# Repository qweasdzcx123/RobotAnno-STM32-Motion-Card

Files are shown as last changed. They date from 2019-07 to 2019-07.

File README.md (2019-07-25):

# RobotAnno-STM32-Motion-Card
## RobotAnno robotic arm
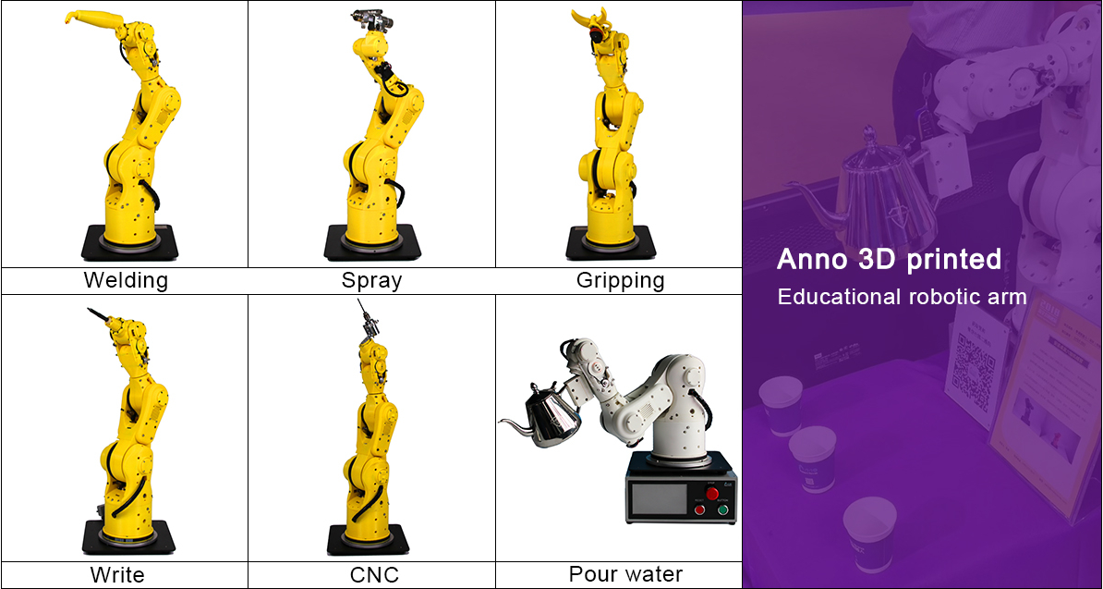
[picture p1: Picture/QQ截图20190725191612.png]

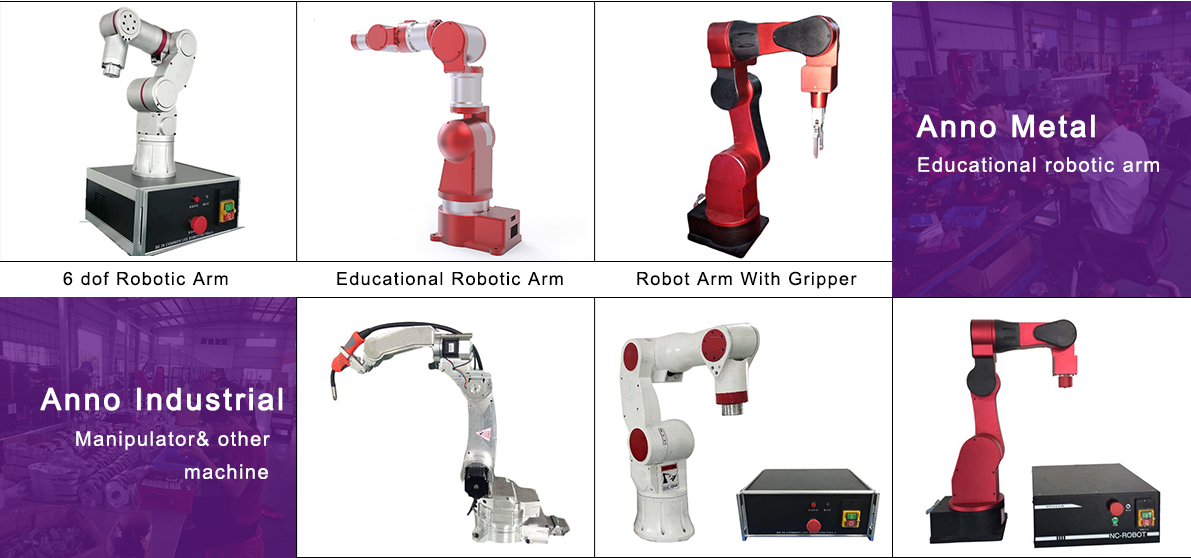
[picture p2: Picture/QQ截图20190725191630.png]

## shop for RobotAnno
https://robotanno.en.alibaba.com/

## introduction
  RobotAnno, a developer and manufacturer of desktop robotics solutions.Through continuous innovation, RobotAnno is committed to providing
educational robots, light industrial robots and service robots with acost-effective, easy-to-use, and best-of-breed revolutionary desktop robot arm product and solution. RobotAnno Robotics Located at the scientific community of academies and makers of desktop robotics, the Robot Anno arm covers the areas of STEAM (science, technology, engineering, math),getting hands-on and hands-on experience in mechanics, electronics , The charm of control systems and computer science. RobotAnno strive to become China and the world's most influential desktop arm business.
## Product Features：
>> Cost-Effective
>>> To meet the same performance,will be the lowest price in the same level,RobotAnno robot arm price level can do a thousand dollars.High performance,called the best of small industrial robotic arm

>> High precision
>>> Multi-axis interpolation control algorithm to ensure that robots with high-precision control

>> Industrial  materials
>>> Using industrial materials as the robot body

>> Multi-function
>>> Support PC, and other intelligent interactive control methods

>> Rich secondary development interface
>>> Provide a serial port,and other rich communication for secondary development
## Control upper computer
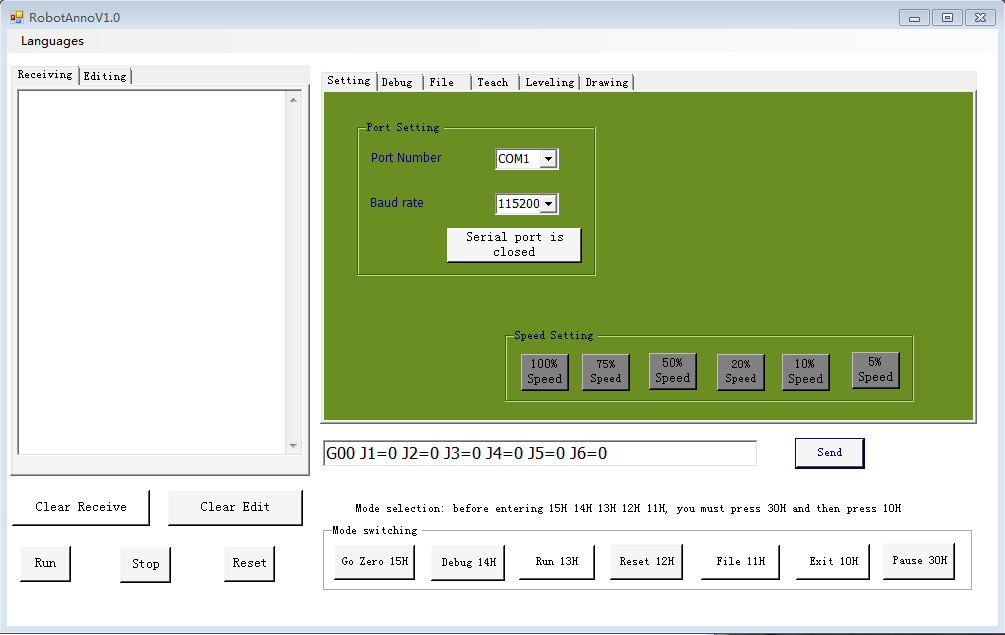
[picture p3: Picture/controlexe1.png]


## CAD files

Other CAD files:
CAD/RobotAnnoV6PLUS_2018-8.STEP
CAD/RobotAnnoV6PLUS_2018-8.SLDPRT

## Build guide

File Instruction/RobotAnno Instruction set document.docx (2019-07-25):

/************************************************* ******************************

* Hardware version: CoreV4D2, BASE-BOARDV61, IO-BOARDV6.2;

* System version: 180521 __lFQY_Core.hex

* Created: 2017.05.04

* Modified time: 2011.06.26

* Author:

* Update content: Cancel G04 command, cancel G24 command,

Increase G00 command, immediate value of absolute value, variable; incremental immediate value, variable

Add 2 formats (angle and radians) Trigonometric operation instructions SIN, COS, TAN, ASIN, ASOS, ATAN

************************************************** *****************************/

1. Serial port instruction

1.1 serial port mode

Serial port parameters: baud rate 115200; data bit 8; stop bit 1.

Instruction format:

The control commands are hexadecimal 0X10 (idle mode), 0X11 (file mode), 0X12 (zero return mode), 0X13 (run mode), 0X14 (debug mode), 0X15 (reset mode); 0X05 is the interrogation mode;

The running instructions all start with 'GXX' and end with a carriage return;

The teaching instruction ends with a carriage return and a new line;

In the system version of 180521 and above, when _flagSoftRst=1 is set in the parameter file, the serial port 1 can send 0X18 to output the output port o14 in any case. According to this function, the e14 relay control NRST restart (emergency stop).

0X05: == query mode ==

The control card is in any working mode (except file mode), and the serial port sends 0X05 to ask the current working mode of the control card. The return value is 0X10, 0X12, 0X13, 0X14, 0X15.

0X10: == enter idle mode ==

When the control card is in idle mode (0X10): it is in idle mode.

In file mode, 0X10 is valid after the file operation instruction is run.

In the zero return mode, the robot stops moving (send 0X30) and sends 0X10 to take effect.

In the running mode, the robot stops moving (send 0X30) and sends 0X10 to take effect.

In reset mode, the reset completes the brake and exits to idle mode. It is in idle mode when it is turned on.

0X11: == enter file mode ==

Download the running file and select “Send File” after sending 0X11. Among them, the first act in the file

"wr=ST" is the run file;

"WR=INI" is a parameter file;

"WR=oq" is a zero return file;

"WR=T_0" is the default run file, equivalent to "wr=ST";

"WR=T_1" is the run 1 file;

"WR=T_2" is the run 2 file;

"WR=T_120" is the run 120 file;

The second behavior file name; the third behavior file length, the length is the file size except the first three lines.

After reading the running file and sending 0X11, send "WR=R,##" ("##" is the length of the read content) to receive the running file.

After reading the parameter file, send "WR=P,##" ("##" is the length of the read content) after sending 0X11 to receive the parameter file.

After reading the parameter file, after sending 0X11, send "WR=Q,##" ("##" is the length of the read content) to receive the zero return file.

The read parameter file can receive the run 0 file after sending 0X11 and sending "WR=H_0,##" ("##" is the read content length).

After reading the parameter file, send "WR=H_1,##" ("##" is the length of the read content) after sending 0X11 to receive the run 1 file.

After reading the parameter file, after sending 0X11, send "WR=H_120,##" ("##" is the read content length) to receive the run 120 file.

0X12: == Motor zero return mode ==

After entering the zero return mode, the system automatically runs the file content and the instructions sent by the serial port in real time. Pause is 0X30, continue to 0X12, exit is 0X10

Instructions can be obtained from the run file and can also be obtained from the serial port.

Automatically exit idle mode after running the contents of the file

0X13: == enter running mode ==

After entering the running mode, the system automatically runs the file content and the instructions sent by the serial port in real time. The pause is 0X30, the continuation is 0X13, and the exit is 0X10.

Instructions can be obtained from the run file and can also be obtained from the serial port.

After running the contents of the file, it automatically runs from the beginning.

0X14: == enter debug mode ==

Send 0X05 as the inquiry mode.

Send 0X10 as the exit mode.

Send "0" to stop and send the angle of each axis of the machine.

Send "SVON=1" for servo enable.

Send "SVON=0" to disable the servo.

Send "SVBM=1" to the servo without holding the brake.

Send "SVBM=0" as the servo brake.

Send "CLR=ST_PUL" to clear the position of the control card.

Send "CLR=SV_ALM" to clear the drive alarm.

Send "J#+" to the #axis angle plus motion (#=1, 2, 3, 4, 5, 6).

Send "J#-" to the ##axis angle minus motion.

Send "J#0" to stop at ##axis angle.

Send "J#<" to repeat the motion for the #axis angle (@0°~ -90°).

Send "J#>" to repeat the motion for the #axis angle (@ 0°~ 90°).

Send "P VE=####" to change the running speed to #### pulses/sec.

Send "P AC=####" to change the acceleration to #### pulses/square sec.

Send "P DE=####" to change the deceleration to #### pulses/square sec.

Send "G00 J#=####,...." to get the robot joints to the appropriate angle.

Send "G07 **=####" to specify parameters for changing the robot.

TX+: Cartesian coordinates X+;

TX-: Cartesian coordinates X-;

TY+: Cartesian coordinates Y+;

TY-: Cartesian coordinates Y-;

TZ+: Cartesian coordinates Z+;

TZ-: Cartesian coordinates Z-;

TA+: Cartesian coordinates A+;

TA-: Cartesian coordinates A-;

TB+: Cartesian coordinates B+;

TB-: Cartesian coordinates B-;

TC+: Cartesian coordinates C+;

TC-: Cartesian coordinates C-;

P CYCP1=800000: The J1 axis is subdivided into 800,000 pulses per week

P J1=24000 Assignment to J1

P=VE Query VE value There are VE, AC, DE, CYCP1,...,J1,...,H0,D1,H2...

0X15: == enter reset mode ==

Return the machine to zero.

2. Button control instructions

When starting up, press the "Start" button to run the robot to run mode.

In the operating mode, at runtime, press the "Stop" button to pause the machine.

In the operating mode, when stopped, press the "Start" button and the machine continues to run.

In the operation mode, when stopping, press the "Stop" button and then press the "Start" button, the machine resets and exits the idle mode.

Instruction description:

//========================================================= ===============

G0n=GGN such as G06 O=P1.1 is equivalent to GG6 O=P1.1

Point-to-point command G00, G20

G00 J1=0 J2=0 J3=-90 J4=0 J5=-90 J6=0 //with acceleration and deceleration absolute joint position command

G00 J1=VXX J2=0 J3=VXX J4=VXX J5=-90 J6=0 //With acceleration and deceleration Absolute joint position command

G00 ... J2'4 J3'VXX ... //with acceleration and deceleration relative joint position command

G00 ... J2'4 J3'VXX J4=VXX J5=-90... //J2 is

G20 X=300 Y=100 Z=500 A=0 B=180 C=0 D=0 //with acceleration and deceleration

G20 X=300 Y=VXX Z=VXX A=VXX B=180 C=VXX D=0 //with acceleration and deceleration

G30 EQ01 J1=UXXXX, J2=UXXXX, J3=UXXXX Read memory contents G30 EQ01 J1=U30100 J2=U30120 J3=U30140 J4=U30160

G30 EQ02 U3060=XX.XX Write memory contents G30 EQ02 U30500=10

G30 EQ03 ASK=UXXXX Query memory contents

G30 EQ04 Vxx=UXXXXXX

G30 EQ05 UXXXXXX=Vxx

G40 X=300 Y=100 Z=500 A=0 B=180 C=0 D=0 //No acceleration/deceleration

Linear command G01 G21

G01 J1=0 J2=0 J3=-90 J4=0 J5=-90 J6=0

G21 X=300 Y=100 Z=500 A=0 B=180 C=0 D=0

G21 X=VXX Y=VXX Z=500 A=0 B=VXX C=0 D=0

G41 X=300 Y=100 Z=500 A=0 B=180 C=0 D=0 //with acceleration and deceleration

G41 X=300 Y=VXX Z=VXX A=0 B=180 C=0 D=0 //with acceleration and deceleration

Arc command G02 G03 G04 G22 G23 G06 DEGREE=ARC (or degree)

When DEGREE=ARC is going to be a three-point arc

Current point: G21 X=200 Y=0 Z=200 A=-180 B=150 C=0 D=0

Second point: G22 X=300 Y=100 Z=200 A=-180 B=150 C=90 D=0

Third point: G23 X=400 Y=0 Z=200 A=-180 B=150 C=300 D=0

Arc running: G06 DEGREE=300

//========================================================= ===============

G06 directive

G06 T=500 delay 500 milliseconds

G06 t=VXX Delay VXX content milliseconds (for example: G08 MOV V400=#2000 G06 t=V400 is a delay of 2000 milliseconds)

G06 I=P1.1 Wait for P1 to be high

G06 I=P2.0 Wait for P2 to be low

G06 O=P1.1 makes output port P1 high (different port from input port)

G06 O=P2.0 makes the output port P2 low

G06 SCAN=I Read input port value, stored in V144-V150 unit

G06 SCAN=O Read output port value, stored in V160-V166 unit

G06 SCAN=RTC Read system clock value and store it in V176-V179 unit

G06 DEGREE=ARC robot takes a three-point arc

G06 DEGREE=35.2 The robot walks 35.2 degrees

G06 REPOS=J# J# Axis looks for HOME# sensor from angle increase direction (return to low level)

G06 REPOS=-J# J# axis finds HOME# sensor from angle reduction direction (return to low level)

G06 REPOS=J1 J1 axis finds HOME0 sensor from angle increase direction (return to low level)

G06 REPOS=-J1 J1 axis finds HOME0 sensor from angle reduction direction (return to low level)

G06 REPOS=JH# J# Axis finds HOME# sensor from angle increase direction (return to high level)

G06 REPOS=-JH# J# axis finds HOME# sensor from angle reduction direction (return to high level)

G06 REPOS=JH1 J1 axis finds HOME0 sensor from angle increase direction (return to high level)

G06 REPOS=-JH1 J1 axis finds HOME0 sensor from angle decrease direction (return to high level)

//========================================================= ===============

G07 command

G07 VE=250000 speed is 250,000 pulses per second

G07 AC=250000 Acceleration is 250,000 pulses per second squared

G07 DE=250000 Deceleration is 250,000 pulses per second squared

G07 VPP=250000 Maximum speed 250,000 pulses per second

G07 VP=20 Speed VE is 20% of the highest speed, VE=VPP*VP*0.01

G07 vp=VXX Speed VE is the content of the highest speed VXX, VE=VPP*VXX unit value *0.01

G07 _h0=xx height change

G07 RCM=1 print run command, 0 does not print run command

G07 GCM=1 is output at right angle coordinates when teaching, 0 is joint coordinate output

G07 MARKPOS_HERE X1=0 Y1=0 X2=100 Y2=100 Template MARK point

G07 MARKPOS X1=10 Y1=10 X2=110 Y2=110 Match MARK point

G07 UNIT=1.0 Interpolation accuracy (in mm)

G07 P J#=XXXX calibration J# axis

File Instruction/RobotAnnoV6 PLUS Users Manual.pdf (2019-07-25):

# Users Manual

# Prepare

## 1) Positioning before power-on

Manually place the machine in the vertical position as follows before turning the power on:

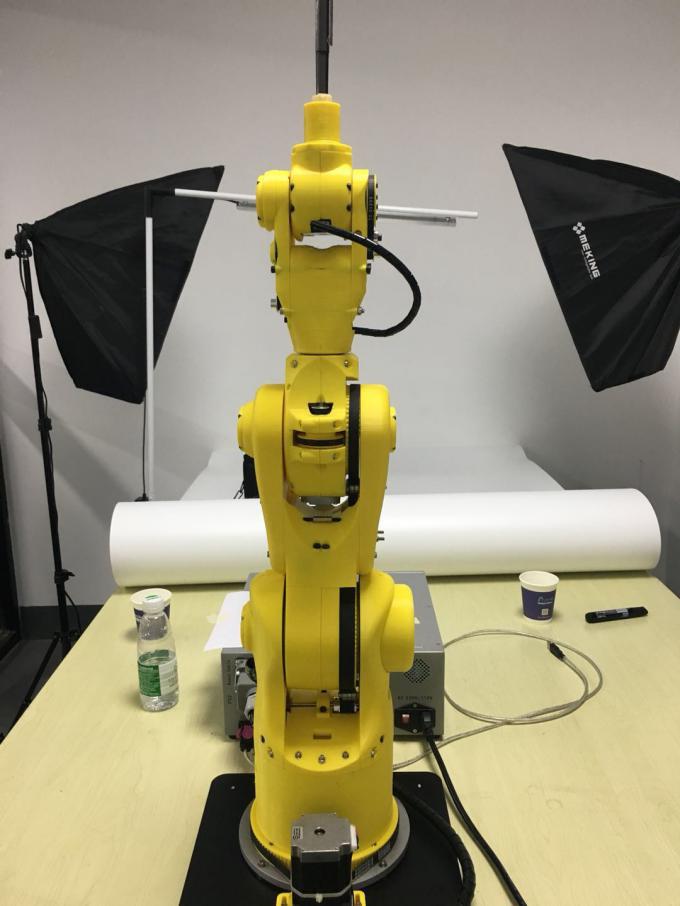
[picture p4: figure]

## 2）Joint position confirmation

After the placement is completed, pay attention to the alignment of the second joint and the third joint arrow, and try to ensure that the machine is in the vertical state, as shown in the following figure:

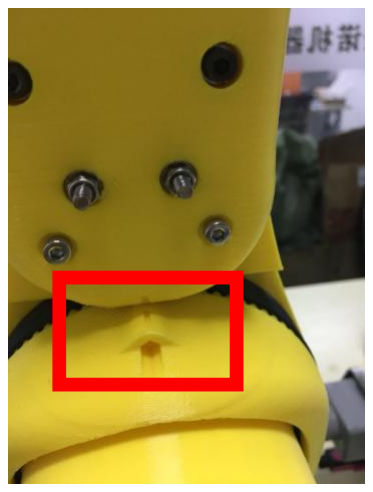
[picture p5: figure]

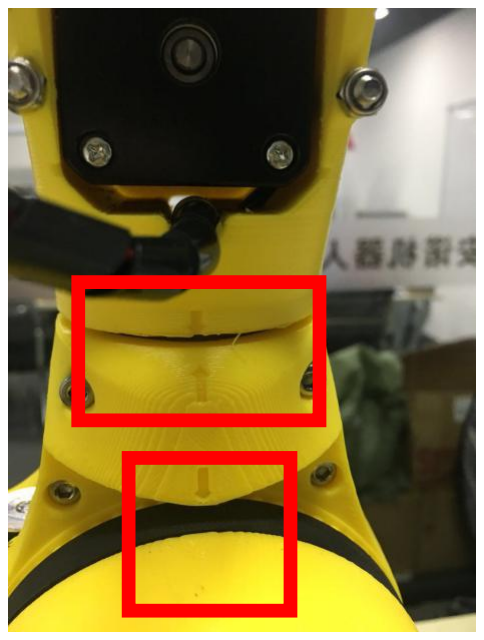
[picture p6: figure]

## 3）Direction confirmation

As shown in the figure below, first confirm whether the direction of each joint movement is consistent with the direction shown in the figure below. Before the machine is shipped from the factory, the direction parameter has been set to OK. If

the direction is inconsistent with the direction shown in the figure during the test, please reset the position of the robot after power off, and then test again. The direction of each joint of the robot must be ensured. Consistent.

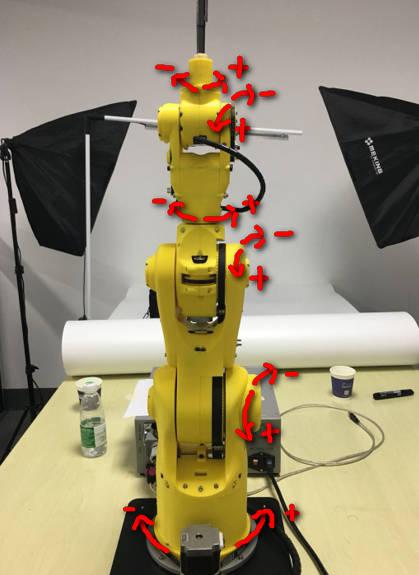
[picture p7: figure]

## 1. Establish a connection

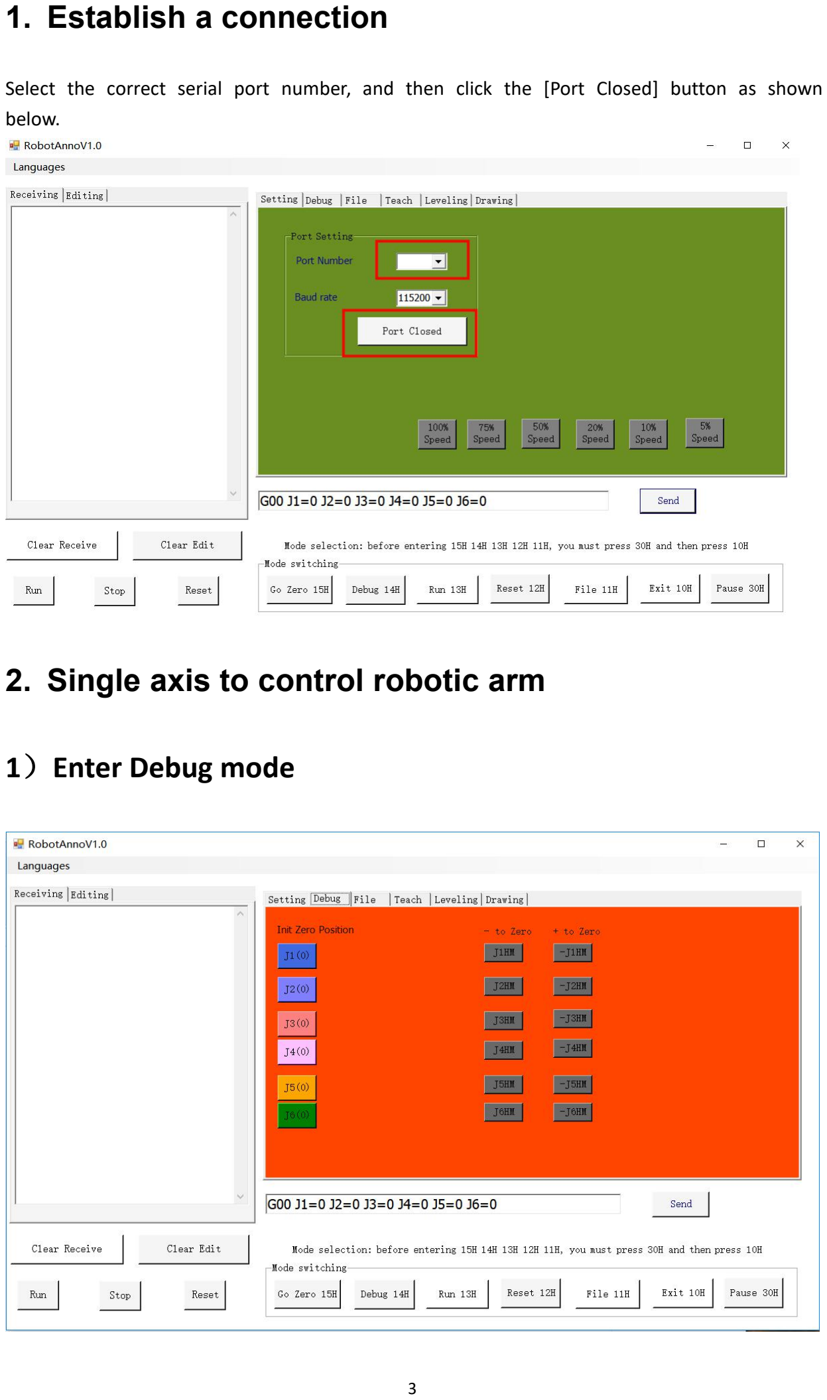
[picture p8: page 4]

Select the correct serial port number, and then click the [Port Closed] button as shown below.

## 2. Single axis to control robotic arm

## 1）Enter Debug mode

## 2）Initialize the position of each joint

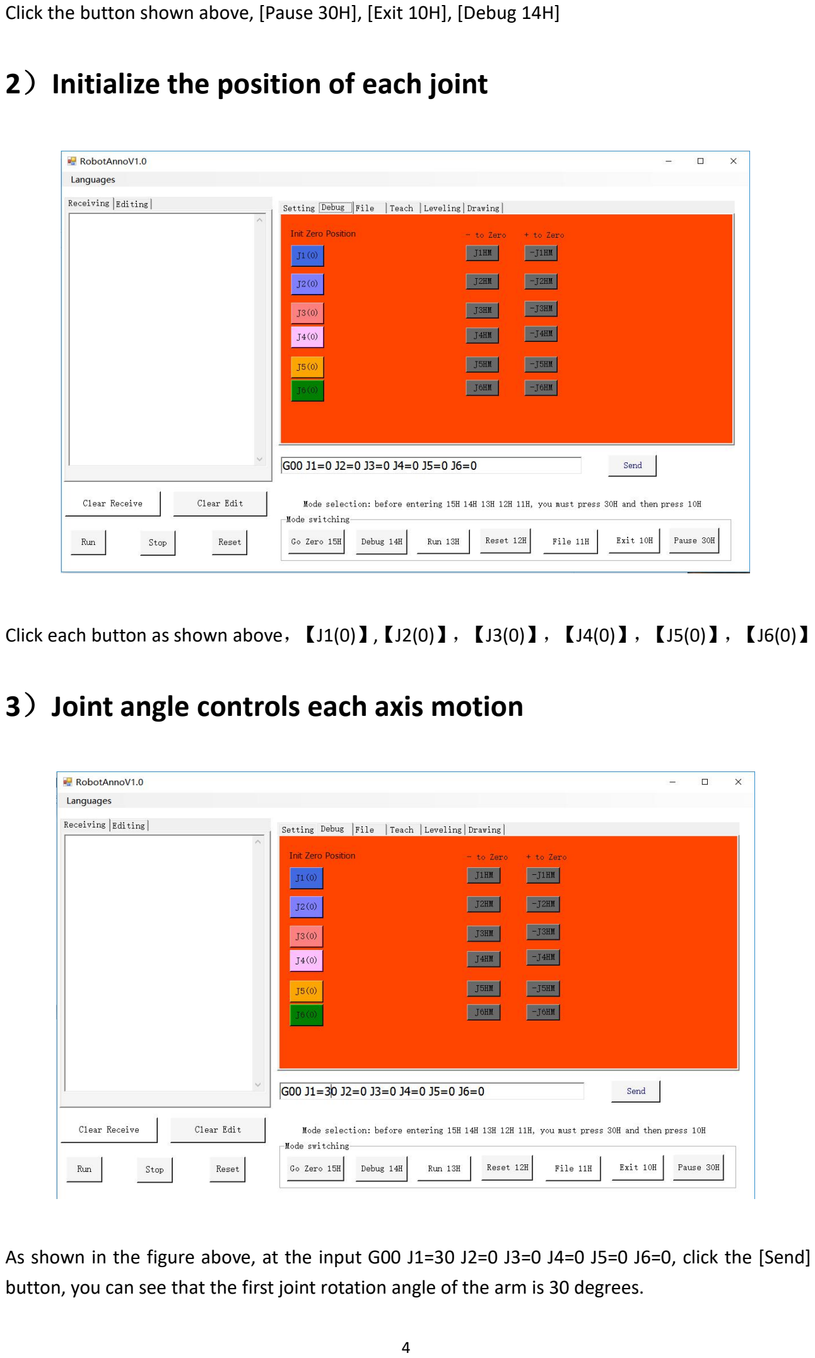
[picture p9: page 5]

Click the button shown above, [Pause 30H], [Exit 10H], [Debug 14H]

Click each button as shown above，【J1(0)】,【J2(0)】，【J3(0)】，【J4(0)】，【J5(0)】，【J6(0)】

## 3）Joint angle controls each axis motion

As shown in the figure above, at the input G00 J1=30 J2=0 J3=0 J4=0 J5=0 J6=0, click the [Send] button, you can see that the first joint rotation angle of the arm is 30 degrees.

note:
1) If only one joint rotation is required, the command G00 J2=20.6 can also be sent. This command indicates that the second axis rotation angle is 20.6 degrees, and the other joints do not move. 2) If you need more than one joint movement, you can send the command G00 J1=20 J2=20

J3=20 J4=20 J5=20 J6=20, this instruction indicates that each joint rotates to 20 degrees. 3) All angle values are absolute angles. The so-called absolute angle, that is, if you send the

command G00 J1=30 and then send G00 J1=30 again, then the second time will not see any action of the arm, because the first command has moved the arm It is 30 degrees. 3. Space coordinate system control arm

premise:
Because our robotic arm is an open-loop solution, it does not have the same amount of feedback as the servo motor, so we need to pay attention to the following points:
1. Before starting the machine, make sure that the arm is in the vertical state. By default, the angle of each joint is 0 at this time. 1. To move the machine to the door position, the command to be executed is: G00 J1=0 J2=0

J3=-90 J4=0 J5=-90 J6=0, after moving to the door position, the command to be executed is: G20 X= 217.4 Y=0 Z=431.1 A=0 B=180 C=0 D=0, the robot will not move at this time. Through this operation, the rotation angles of the respective axes in the controller are matched with the spatial coordinate values.

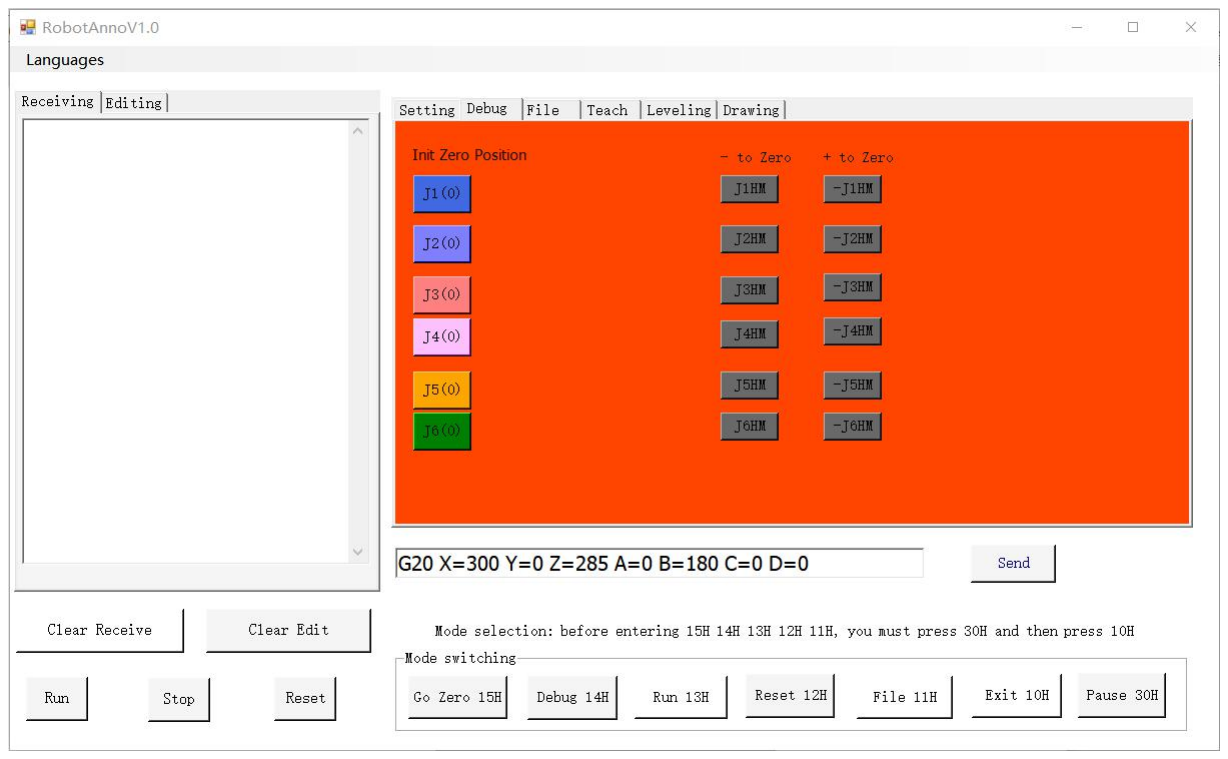
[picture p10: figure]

Before doing this, be careful to use debug mode. As shown above: Input command G20 X=300 Y=0 Z=285 A=0 B=180 C=0 D=0, click the [Send]

button to move the end of the robot arm to (300, 0, 285) The spatial coordinate position.

## 4. Execution file

## 1）Enter file mode

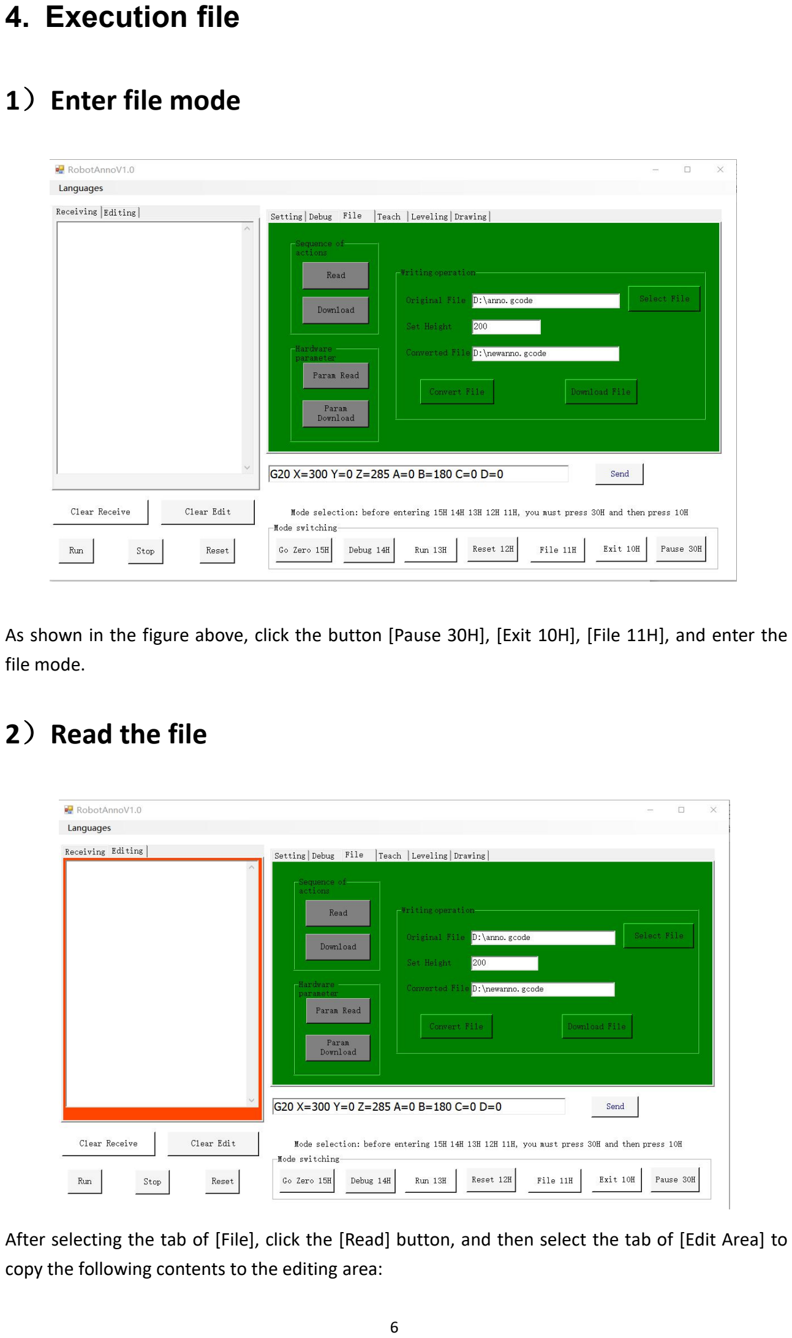
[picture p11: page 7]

As shown in the figure above, click the button [Pause 30H], [Exit 10H], [File 11H], and enter the

## file mode. 2）Read the file

After selecting the tab of [File], click the [Read] button, and then select the tab of [Edit Area] to copy the following contents to the editing area:

FILE=ST
AM.ST
216
code:
G00 J1=0 J2=0 J3=-90 J4=0 J5=-90 J6=0
G20 X=217.4 Y=0 Z=431.1 A=0 B=180 C=0 D=0 G20 X=300 Y=0 Z=285 A=0 B=180 C=0 D=0 G20 X=400
G20 Y=100
G20 X=300
G20 Y=0
G20 X=217.4 Y=0 Z=431.1 A=0 B=180 C=0 D=0

The contents of the above document achieve a continuous motion of a square track. FILE=ST indicates the file type

AM.ST indicates the name of the file. 216 indicates the number of bytes of the file

Code: the rest of the code is the run command
“FILE=ST

AM.ST
216
code: “This part is the file header. Every executable file can be run like this. 216 bytes can be filled with a

number first. After downloading, the controller will calculate a correct number of bytes to fill. 3）Download file to controller

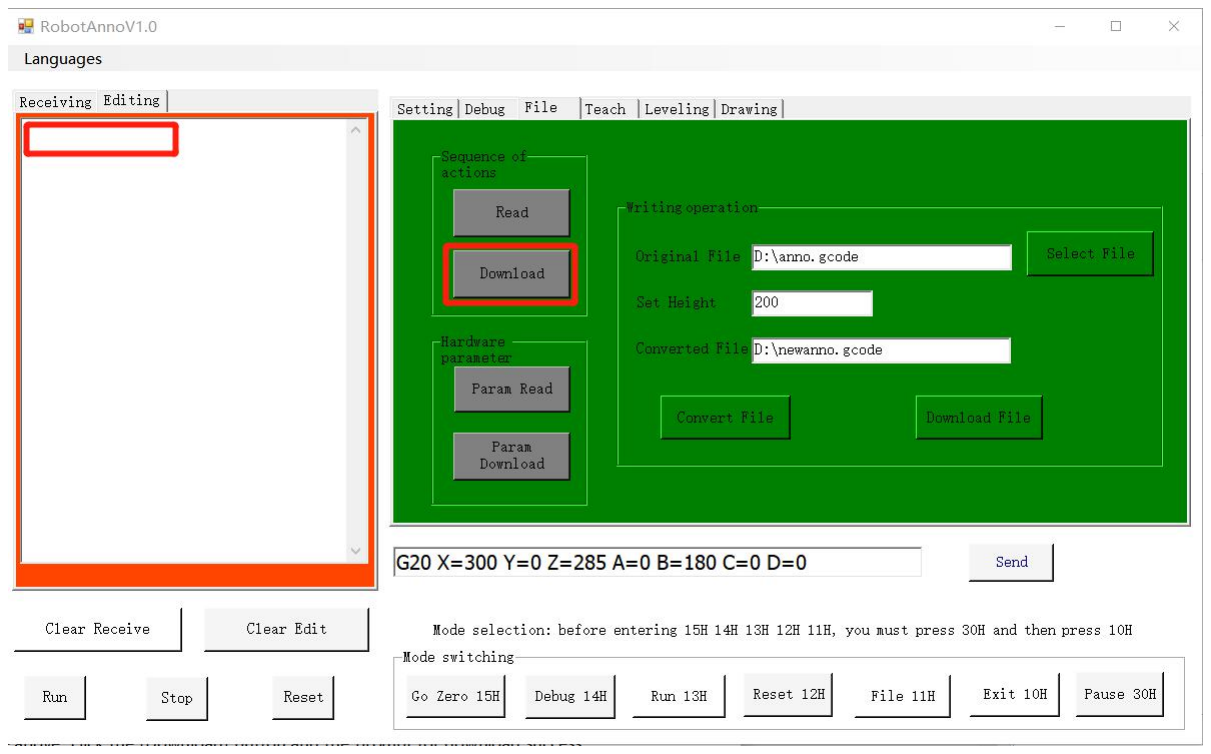
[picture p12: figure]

As shown in the figure above, click the [Download] button and the prompt for download success will be displayed at the location shown in the editing area. 4）Running file

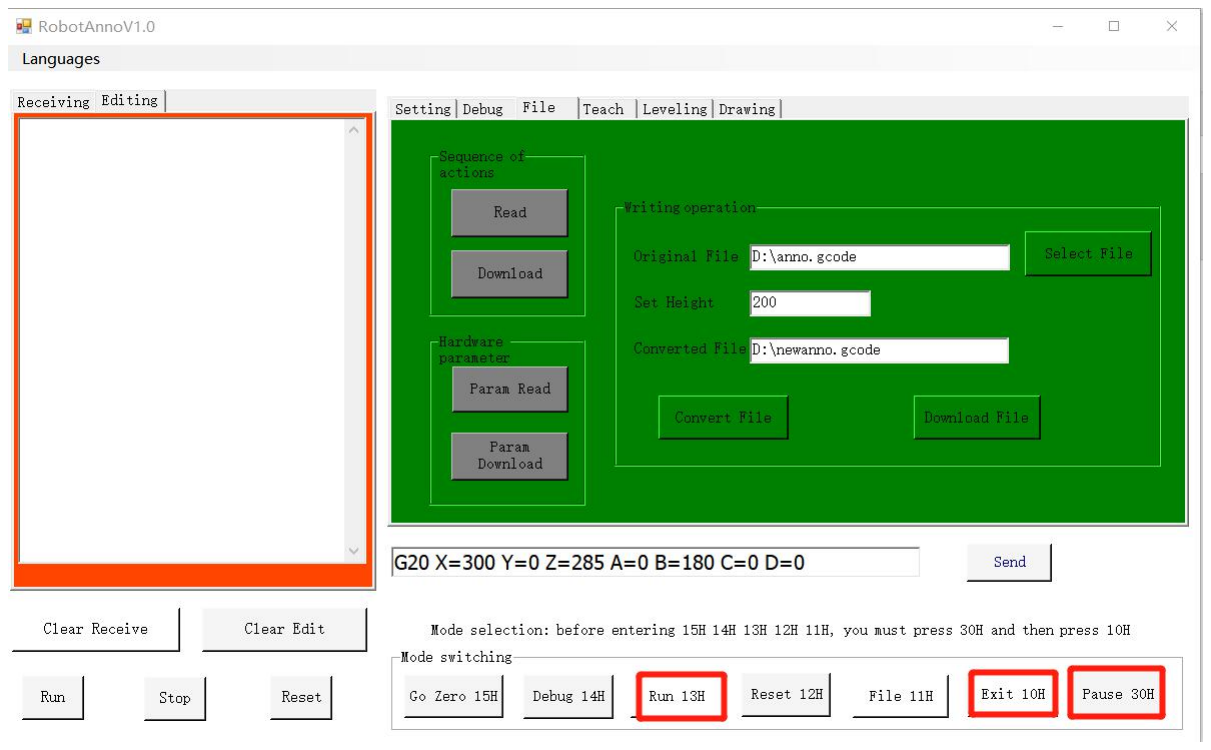
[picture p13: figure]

As shown in the figure above, click the button [Pause 30H], [Exit 10H], [Run 13H], and you can see the movement of the arm. For the file to run, the arm will continue to move and will not stop automatically. 5）Stop file running

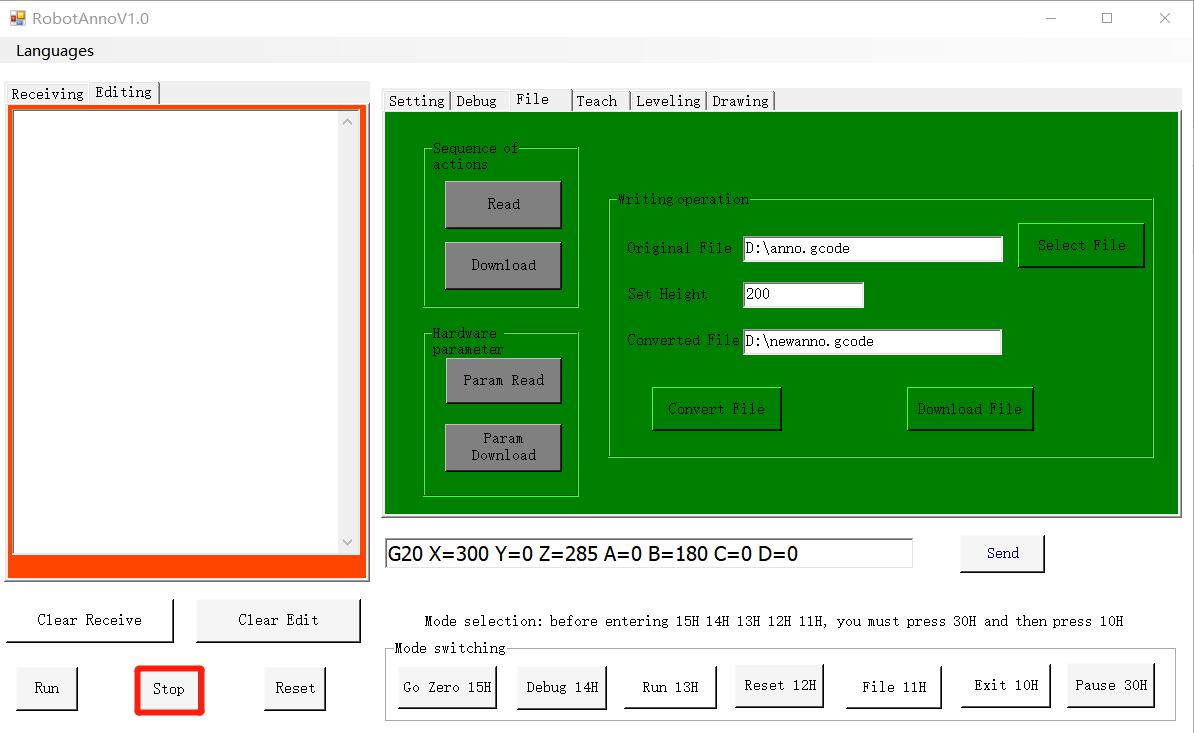
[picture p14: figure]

As shown in the figure above, when the file is running, if the arm is always moving and you need to stop the movement, click the [Stop] button and the arm will stop moving.

## 6）Resume file movement

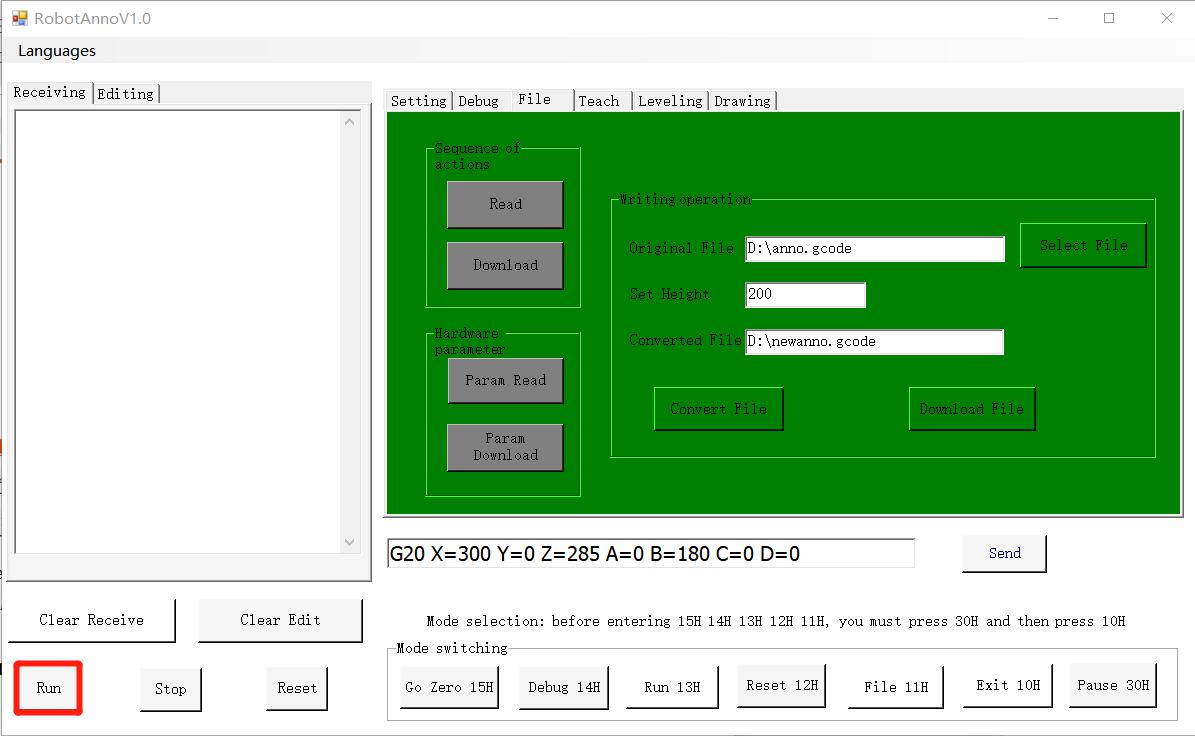
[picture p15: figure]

As shown in the figure above, after stopping the file movement, if you need to continue the movement of the previously stopped file movement, click the [Run] button, you can see that the robot arm continues to move at the position where it stopped before. 7）The arm returns to the zero position

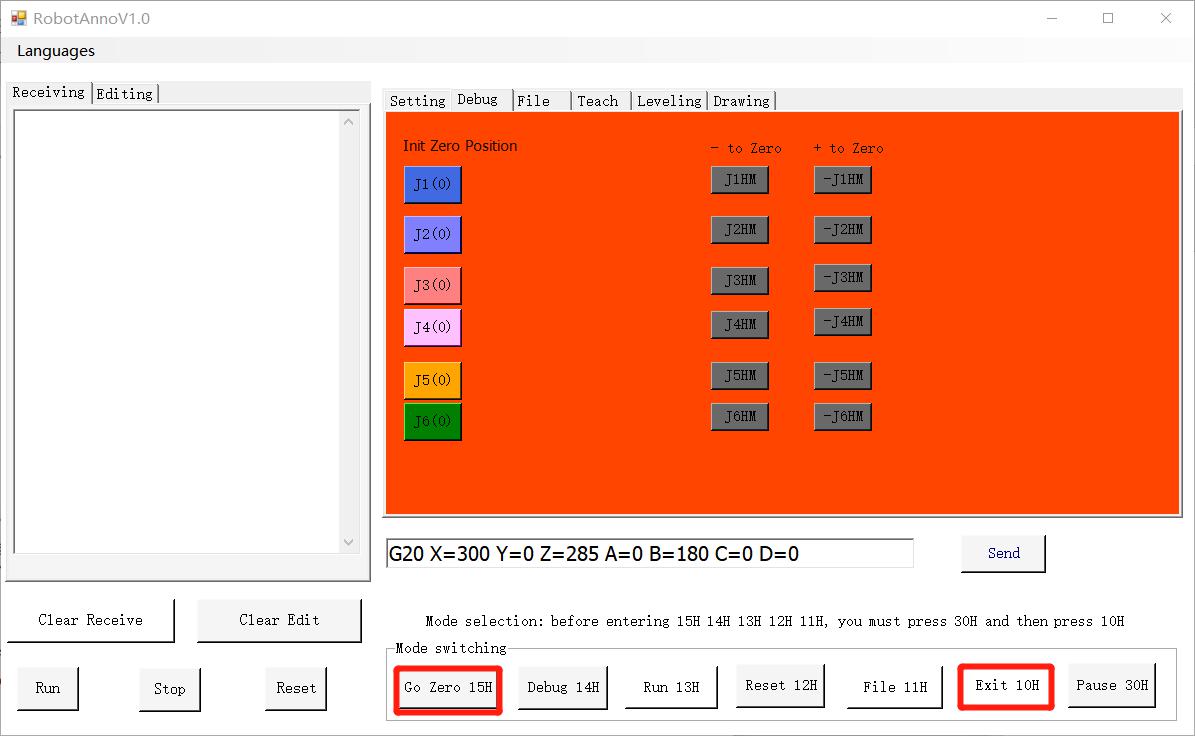
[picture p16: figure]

As shown in the figure above, if you need the arm to return to the zero position (vertical position), click [Pause] -> [Exit] -> [Return to zero], the arm will move to the vertical position. After clicking the above three buttons, if the arm does not move, click the three buttons in turn.

## 5.Adjust the speed

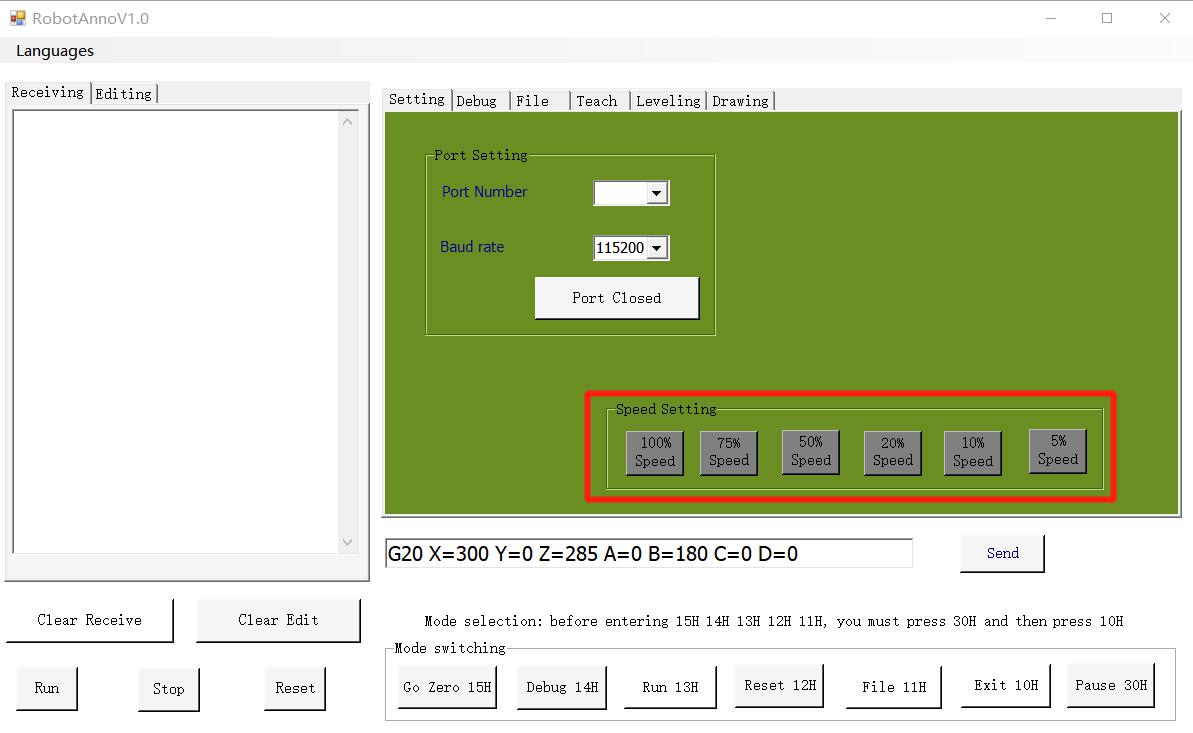
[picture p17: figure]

As shown above, the row of buttons adjusts the speed of the arm movement. note:

1) If the button for adjusting the speed is pressed while the file is moving, then in the subsequent movement, it will run at the speed you set. 2) If a button for adjusting the speed is pressed before executing a single command, the next

motion command will move at the speed you set. 6. Clear operation

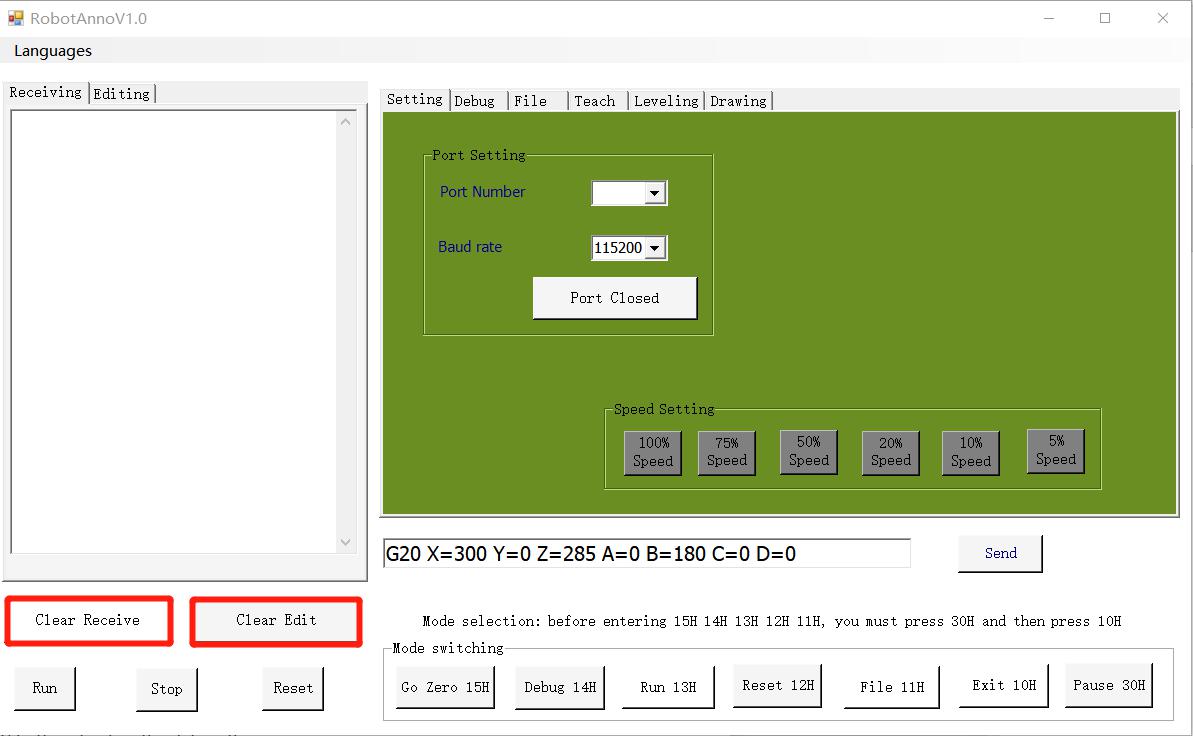
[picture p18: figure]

As shown in the figure above, if there is more data in the [Receive Area], you can press the [Clear Receive] and [Clear Edit] buttons to clear the data in the receive area.

## 7. Writing

## 1）Enter file mode

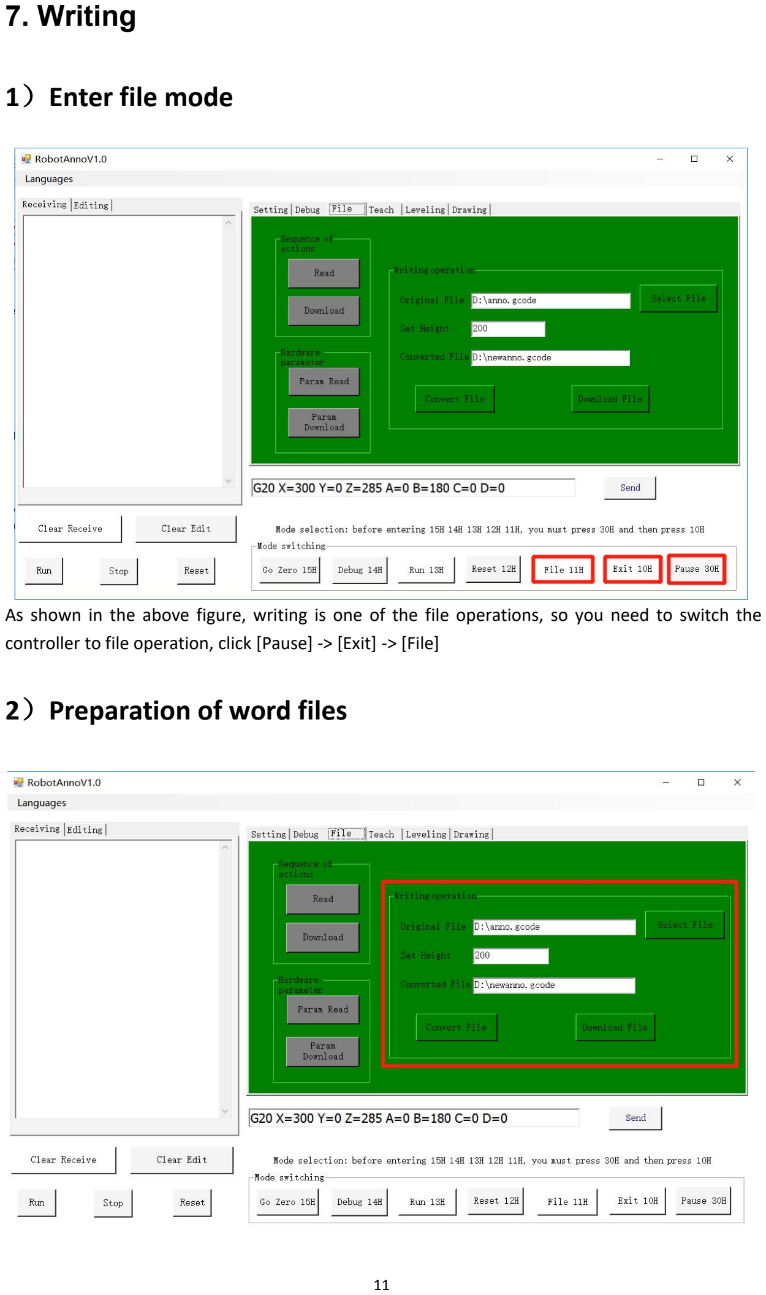
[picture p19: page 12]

As shown in the above figure, writing is one of the file operations, so you need to switch the controller to file operation, click [Pause] -> [Exit] -> [File]

## 2）Preparation of word files

As shown in FIG:
Original file: is a g code file generated using inkscape
Height setting: the height of the writing position
Converted file: is a written file that the robot arm can recognize

First select the original file, then set the height of the writing, click [Convert File], switch the left area to [Edit Area], you can see the converted file content; click [Download Data], if the execution is successful, it will be on the left [Edit Area] displays the prompt "Download Successful". 3）Perform writing

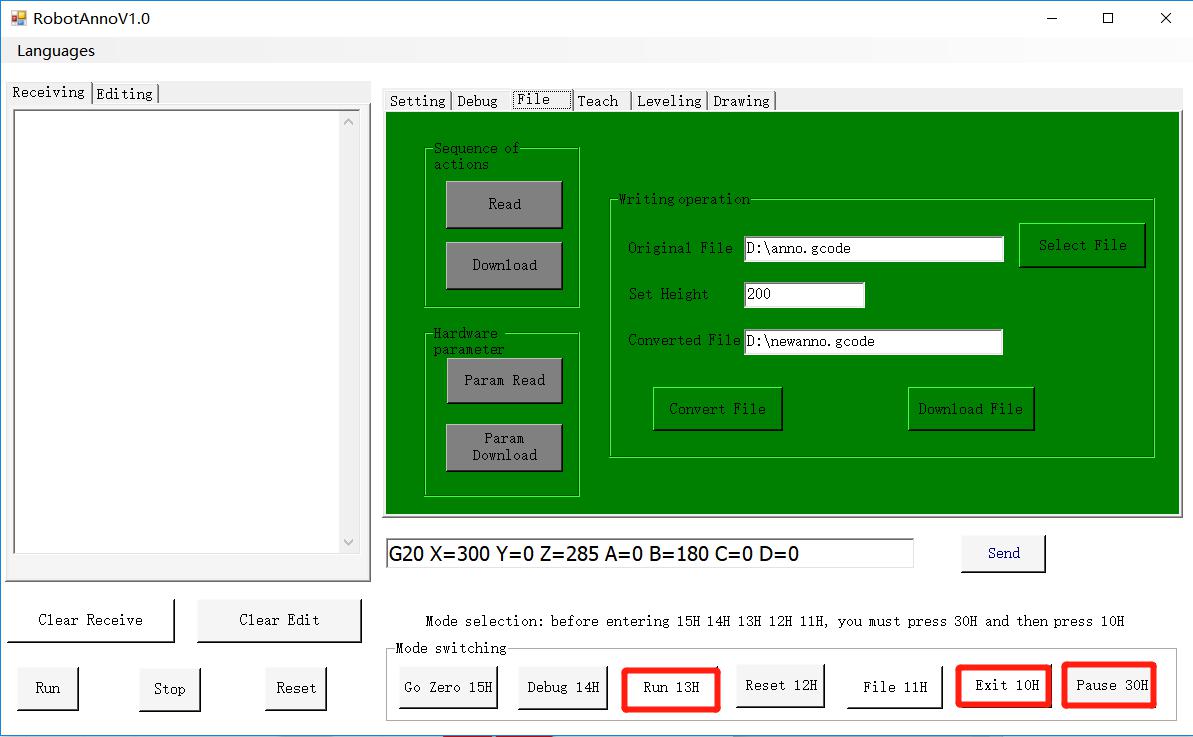
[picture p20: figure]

As shown in the figure above, click [Pause] -> [Exit] -> [Run], the robot arm will start writing. Please note: In the process of writing, there may be cases where some words cannot be written

and some words are too thick. This situation arises because of the inaccuracy of the zero position of the arm. The zero position of the arm needs to be re-adjusted.

## 8. Check the current position of the arm

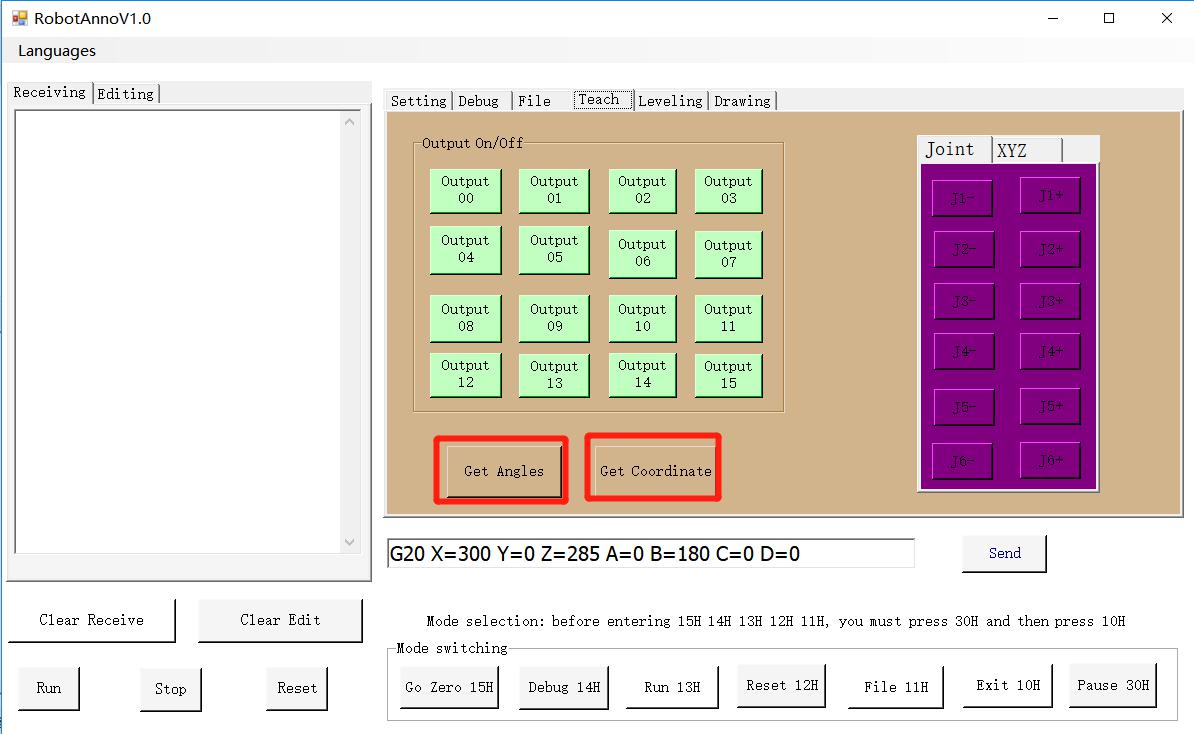
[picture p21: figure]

As shown in FIG:
View the joint rotation angle position of the arm, click [Joint Output], and then click [Pause 30H]. In the [Receive Area], you can see the rotation angle of each joint. View the spatial coordinate position of the arm, click [Coordinate Output], and then click [Pause

30H]. In the [Receive Area], you can see the position of the space coordinate. 9. Robot arm zero leveling

After the robot arm is powered up, before the application action (such as writing, drawing, etc.) is performed, in order to allow the robot arm to reach a relatively accurate absolute position, at this time, the robot arm needs to be zero-leveled. 1）Movement to door position

First set to debug mode, as shown below, click [Pause] -> [Exit] -> [Debug]

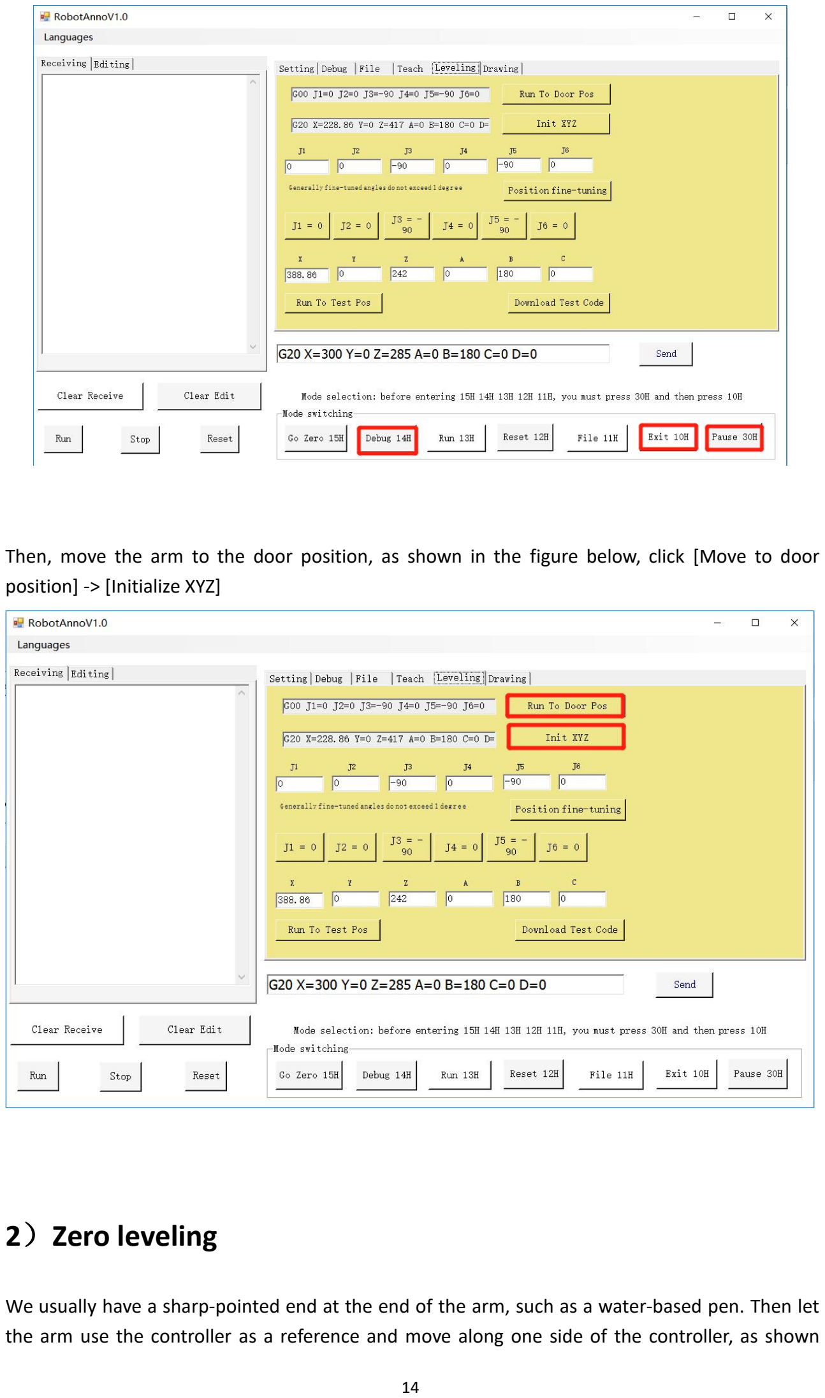
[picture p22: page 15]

Then, move the arm to the door position, as shown in the figure below, click [Move to door position] -> [Initialize XYZ]

## 2）Zero leveling

We usually have a sharp-pointed end at the end of the arm, such as a water-based pen. Then let the arm use the controller as a reference and move along one side of the controller, as shown

below:

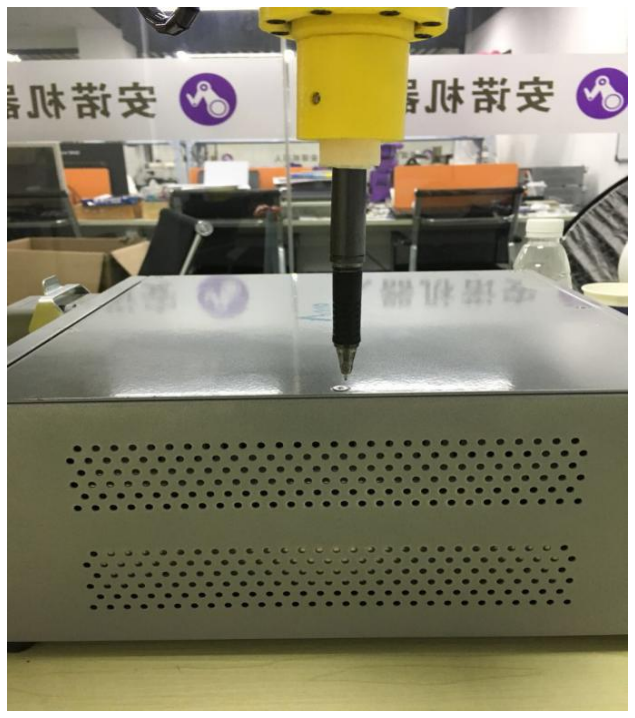
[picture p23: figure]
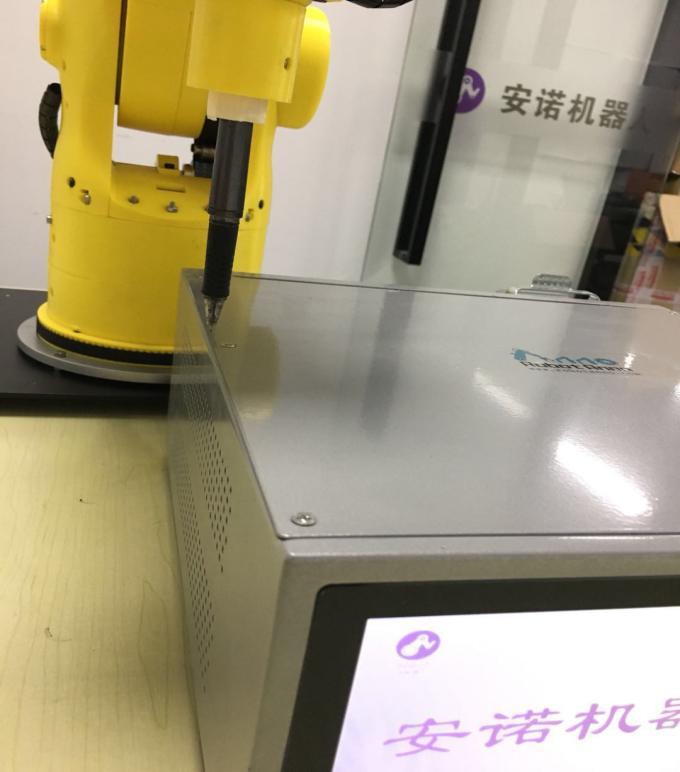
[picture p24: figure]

Leveling in the X direction:
1. As shown in the figure below, after adjusting Z and Y to an appropriate value, only change the value of X, increase or decrease by 20 each time, and let the arm move in the X-axis direction.
It is necessary to observe carefully: as X increases or decreases by 20 each time, whether the end will appear downward or upward. If this happens, the zero position needs to be adjusted.

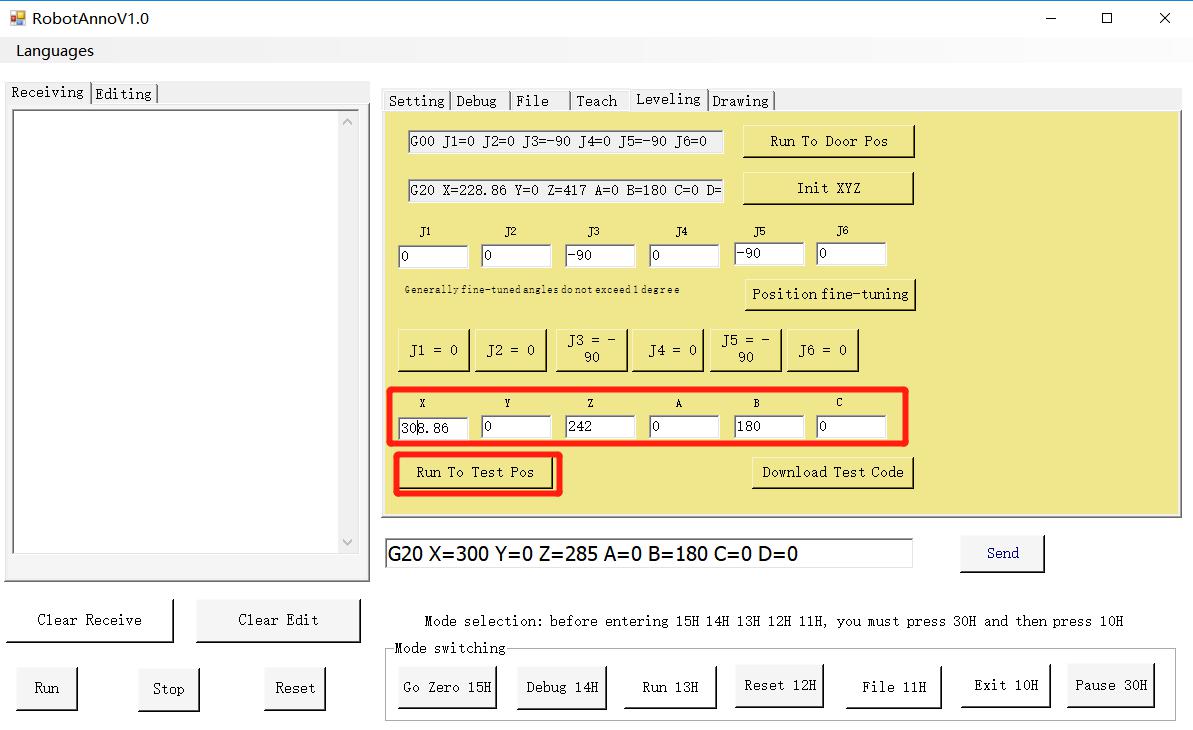
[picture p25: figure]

2. When the zero point needs to be adjusted, return the arm to the door position. As shown in the figure below, click [Move to door position] -> [Initialize XYZ]

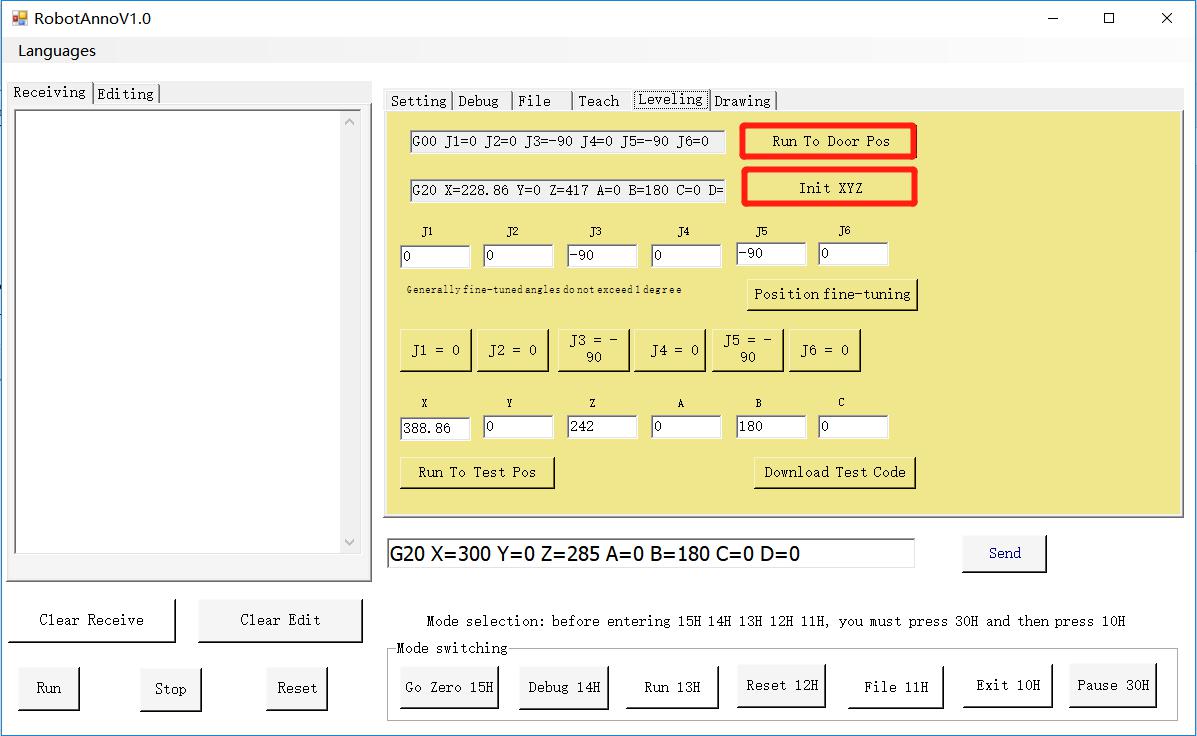
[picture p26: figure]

3. Adjust the zero position
Common situation: When X increases, the end sinks; when X decreases, the end rises.
In this case, the joints that need to be adjusted are two, three, and five joints. In the door position, the above common situation occurs. Generally, the second joint or the third joint is required to be lifted up. Generally, the 0 of J2 is changed to 0.5, and the -90 of J3 is modified to -89.5, so that the effect of lifting upward is achieved. In general, fine tuning will not exceed 1 degree. At the door position, you need to pay attention to whether the arrows of each joint are aligned. If

there is no alignment, please adjust accordingly. As shown in the figure below, modify the corresponding value to fine tune the position. The

specific operation is:
Modify the values corresponding to J1, J2, J3, J4, J5, and J6, and click [Location Fine Adjustment] to move the machine to the corresponding position.

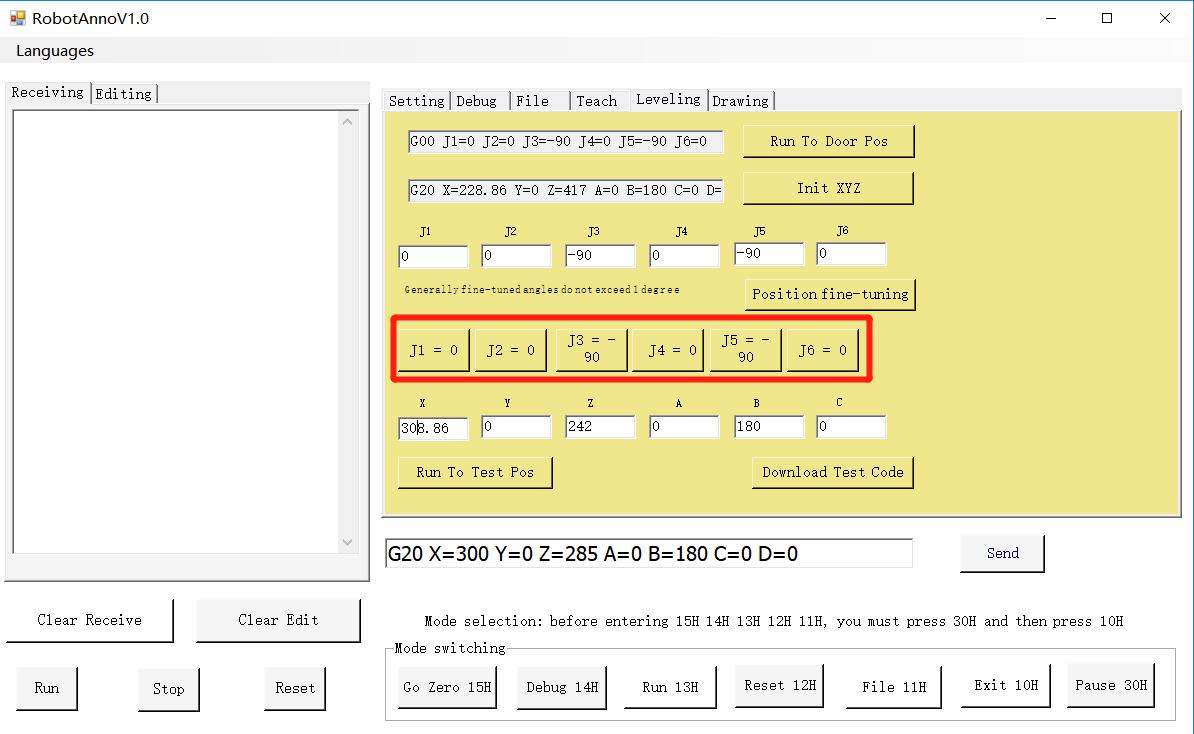
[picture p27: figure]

After fine tuning, you need to set the machine position to zero position, as shown below, do the following:
Click [J1 = 0], [J2 = 0], [J3 = -90], [J4 = 0], [J5 = -90], [J6 = 0]

Then, the leveling in the X direction is performed, and the above steps are sequentially cycled until the X-axis direction is increased or decreased by 20, and the end of the arm is observed within the range of the mechanical arm reachable [228.86, 388.86]. There will be a situation of sinking or lifting, that is, the leveling in the X-axis direction is completed. The leveling in the Y-axis direction is the same as the leveling in the X-axis direction, except that

when fine-tuning, the first and fourth joints need to be adjusted.

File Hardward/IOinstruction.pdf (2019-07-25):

# RobotAnnoV6PLUS

## --IO port wiring and instructions for use 一．Hardware indication:

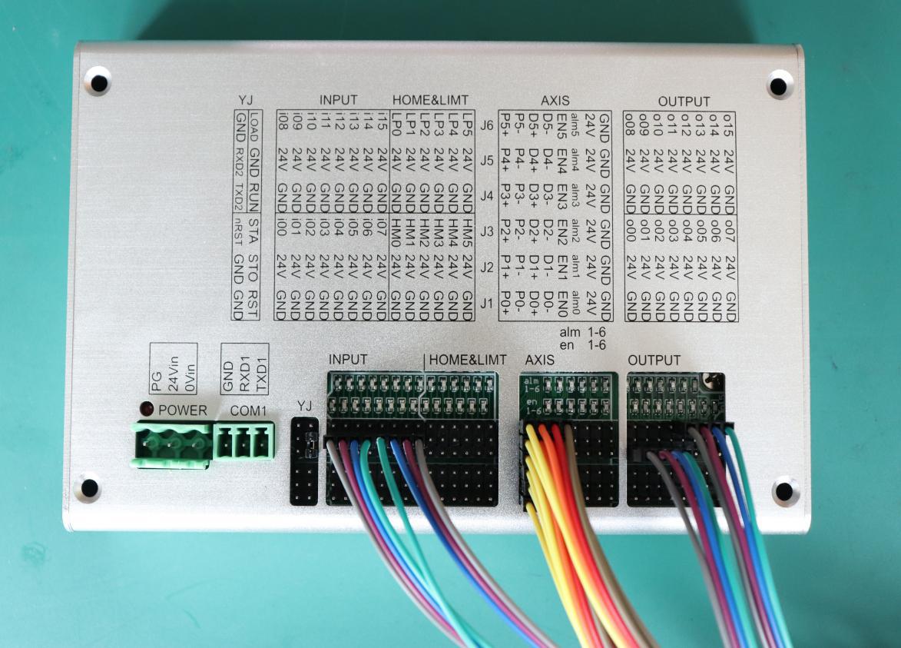
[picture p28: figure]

The input and output ports each have 15 sets of signal ports, and the pins correspond to the left schematic diagram one by one. 二、Introduction to IO port

I00-i15: indicates that the input port 0-15 receives the signal input port, the default state of the input port is high, and if the state is to be changed, a low-level signal input is required. There are two wiring schemes to change its status

The first scheme: one end of the key is connected with an input port, and the other end of the key is connected with the same GND. The touch switch can change the state of the input port to be low. The second scheme uses a single-chip computer or a signal generator to connect the

signal receiving end of the relay, and the relay switch enables the signal input port and the same horizontal row GND respectively. When the relay accepts the enable signal, the input port can be connected to the GND to change the function of

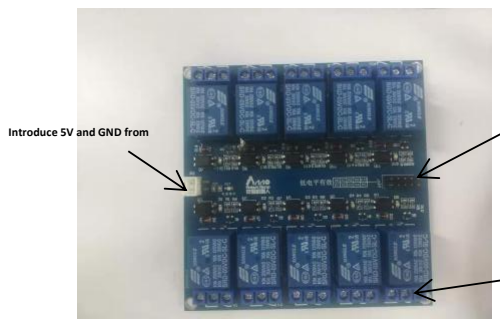
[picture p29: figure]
Introduce 5V and GND from

changing the state of the input port.
Identification signal code: G06I = P1.1 program will always wait for P1 to be high G06I=P1.0 program will always wait for P1 to be low. O00-O15: indicates that the output port 0-15, that is, the signal transmission port, the signal transmission port defaults to a low level, and if it is to change its output

high level, only the code is required to change its output state. It is also noted that the signal receiving terminal needs to co-operate with the control box at the same time, otherwise the signal cannot be identified. Output signal code: G06 O=P1.1 makes output P1 high level (different from input

port)

G06O = P1.0 causes the output port P1 to be low

Signal receiver

Connect the IO port and GND, and the IO port is connected to the left and the GND is connected to the

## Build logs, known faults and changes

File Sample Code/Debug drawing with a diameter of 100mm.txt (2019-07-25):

FILE=ST
AM.ST
310
code: 
G00 J1=0 J2=0 J3=-90 J4=0 J5=-90 J6=0
G20 X=300 Y=0 Z=285 A=0 B=180 C=0 D=0
G21 X=300 Y=0 Z=285 A=0 B=180 C=0 D=0
G22 X=350 Y=50 Z=285 A=0 B=180 C=0 D=0
G23 X=300 Y=100 Z=285 A=0 B=180 C=0 D=0
G06 DEGREE=360
G00 J1=0 J2=0 J3=-90 J4=0 J5=-90 J6=0

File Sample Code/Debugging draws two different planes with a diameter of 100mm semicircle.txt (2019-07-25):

FILE=ST
AM.ST
216
code: 
G00 J1=0 J2=0 J3=-90 J4=0 J5=-90 J6=0
G20 X=217.4 Y=0 Z=431.1 A=0 B=180 C=0 D=0
G20 X=300 Y=50 Z=290 A=0 B=180 C=0 D=0
G21 X=300 Y=50 Z=290 A=0 B=180 C=0 D=0
G22 X=350 Y=0 Z=290 A=0 B=180 C=0 D=0
G23 X=300 Y=-50 Z=290 A=0 B=180 C=0 D=0
G06 DEGREE=180
G20 X=230 Y=-50 Z=290 A=0 B=180 C=0 D=0
G20 X=260 Y=-55 Z=255 A=-15 B=84 C=180 D=1
G21 X=260 Y=-55 Z=255 A=-15 B=84 C=180 D=1
G22 X=255 Y=0 Z=200 A=0 B=84 C=180 D=1
G23 X=260 Y=55 Z=245 A=20 B=84 C=180 D=1
G06 DEGREE=180
G20 X=217.4 Y=0 Z=431.1 A=0 B=180 C=0 D=0

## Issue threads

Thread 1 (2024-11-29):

Window10 Compatibility Problems

FAB619, 2024-11-29:
Hi, I have the Metal version of RobotAnno 6 axis Robot arm SJ602 and I couldn't control it with the application provided, I figured out later that the DLL provided and the application worked with Window 7 and Windows 10 didn't run it.
Is there any updates that I shoud install or is there a compatible version with Windows10.
Thanks in advance.

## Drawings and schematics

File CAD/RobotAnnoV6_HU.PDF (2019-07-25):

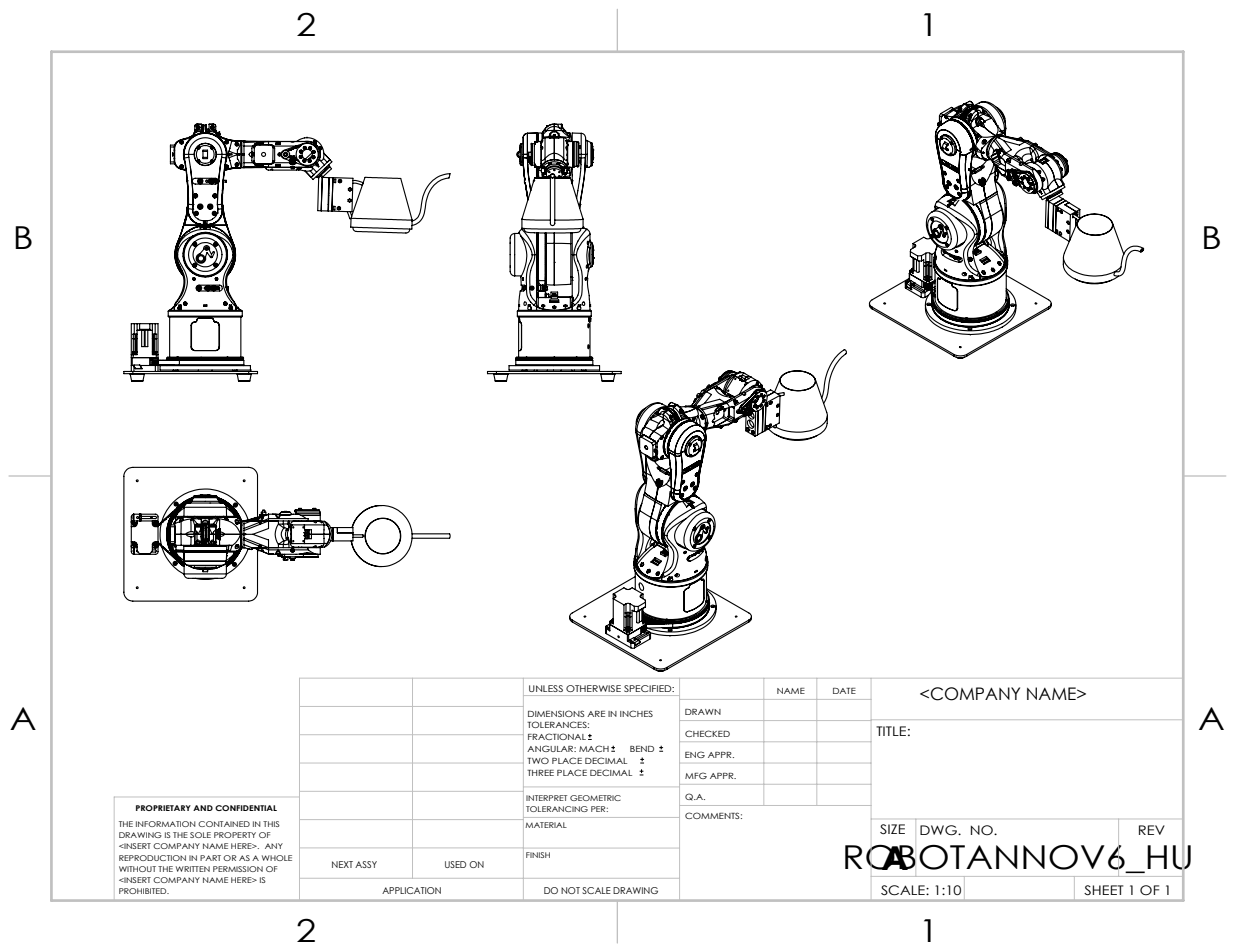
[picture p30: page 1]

UNLESS OTHERWISE SPECIFIED: | | NAME | DATE | <COMPANY NAME>

DIMENSIONS ARE IN INCHES TOLERANCES: FRACTIONAL ANGULAR: MACH BEND TWO PLACE DECIMAL THREE PLACE DECIMAL | DRAWN

CHECKED | | | TITLE:

ENG APPR.
MFG APPR.

INTERPRET GEOMETRIC TOLERANCING PER: | Q.A.

PROPRIETARY AND CONFIDENTIAL
THE INFORMATION CONTAINED IN THIS
DRAWING IS THE SOLE PROPERTY OF
<INSERT COMPANY NAME HERE>. ANY
REPRODUCTION IN PART OR AS A WHOLE
WITHOUT THE WRITTEN PERMISSION OF
<INSERT COMPANY NAME HERE> IS
PROHIBITED.

USED ON | MATERIAL | | SIZE A | DWG. NO. | REV

NEXT ASSY | | FINISH

APPLICATION | DO NOT SCALE DRAWING | | SCALE: 1:10 | | SHEET 1 OF 1

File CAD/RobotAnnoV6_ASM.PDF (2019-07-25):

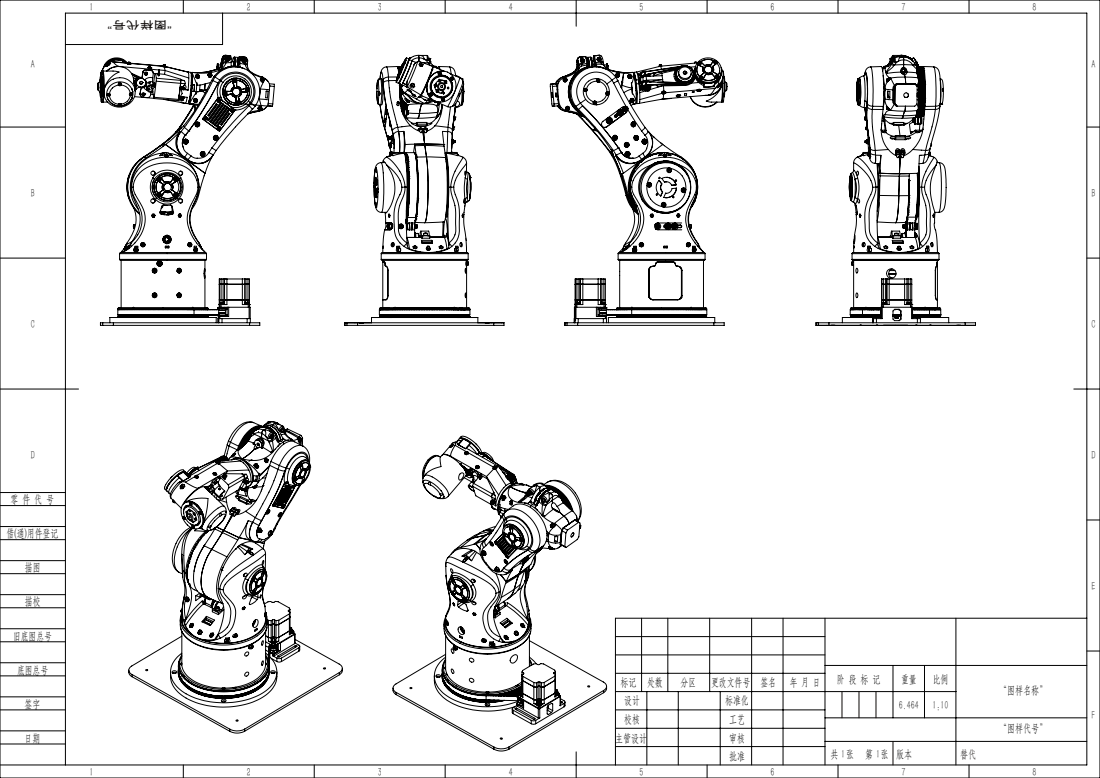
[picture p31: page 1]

阶 段 标 记 | 重量 | 比例 | “图样名称”

标记 | 处数 | 分区 | 更改文件号 | 签名 | 年 月 日
设计 | | | 标准化 | | | | | 6.464 | 1:10
校核 | | | 工艺
主管设计 | | | 审核

“图样代号”

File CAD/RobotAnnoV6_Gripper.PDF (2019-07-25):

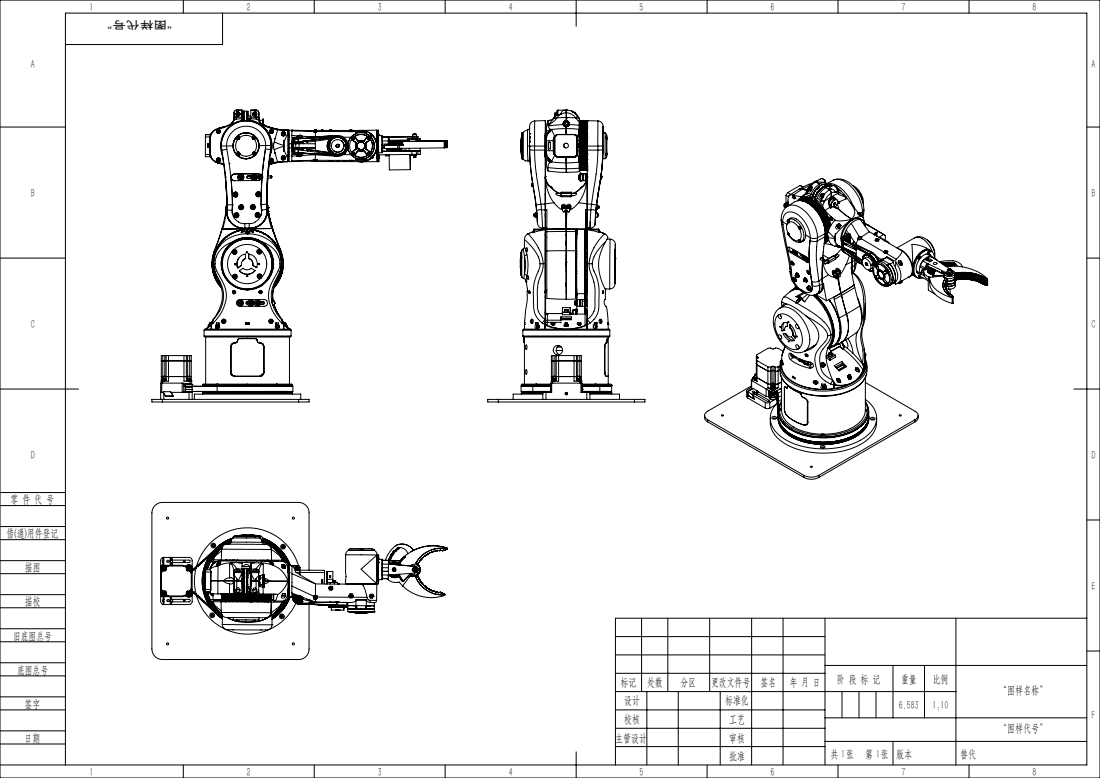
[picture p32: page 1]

阶 段 标 记 | 重量 | 比例 | “图样名称”

标记 | 处数 | 分区 | 更改文件号 | 签名 | 年 月 日
设计 | | | 标准化 | | | | | 6.583 | 1:10
校核 | | | 工艺
主管设计 | | | 审核

“图样代号”

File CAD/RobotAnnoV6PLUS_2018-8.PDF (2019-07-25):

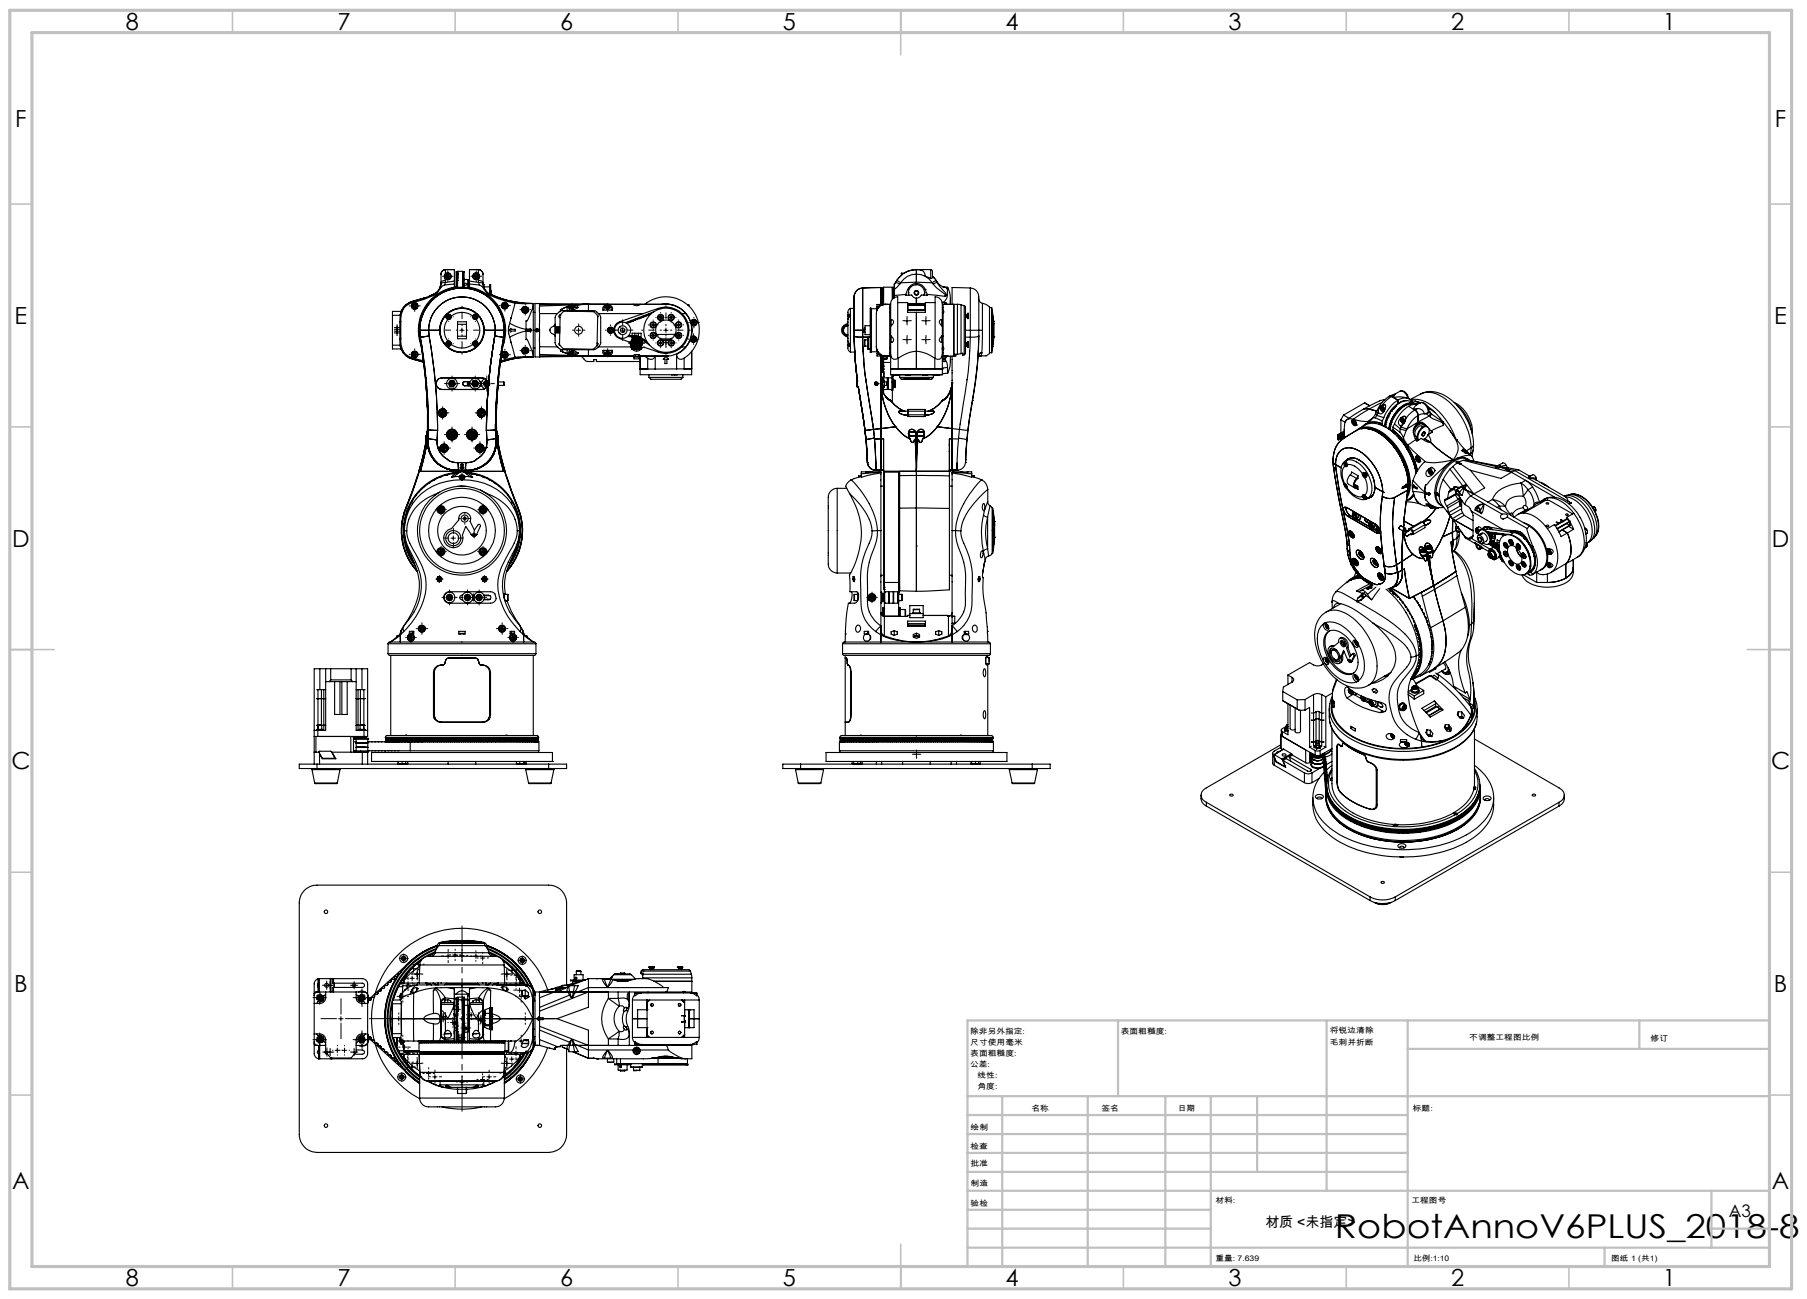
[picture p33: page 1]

绘制
检查
批准
制造
验检 | | | | 材料: | 工程图号 | A3 材质 <未指定>

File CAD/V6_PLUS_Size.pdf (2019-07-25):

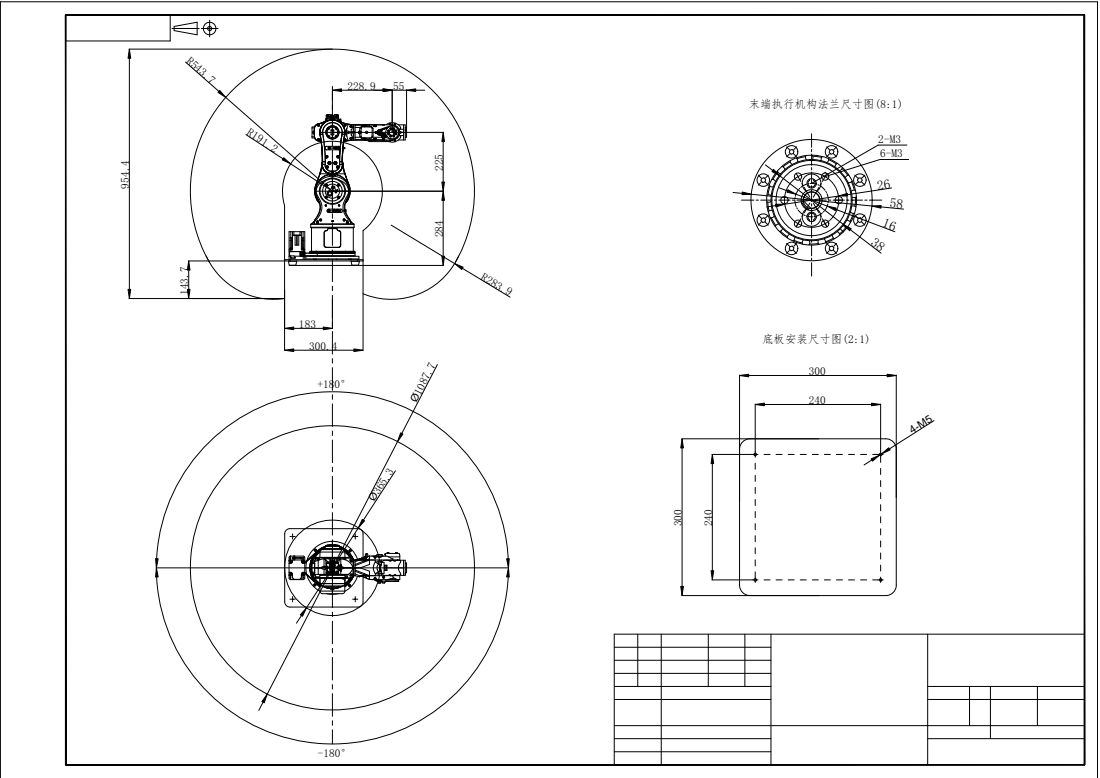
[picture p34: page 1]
末端执行机构法兰尺寸图(8:1); 底板安装尺寸图(2:1)

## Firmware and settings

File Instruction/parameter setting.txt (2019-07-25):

FILE=INI
Parameter.ini
511
////DH_PARAMETER:
_h0=242;
_d1=0.1;
_h2=225;
_d3=0.1;
_h4=228.86;
_h5=50;
_d6=16;
////MOTOR_DIR:
_dir1=-1;
_dir2=-1;
_dir3=-1;
_dir4=-1;
_dir5=1;
_dir6=1;
////JOINT_PUL:
_j1pul=172800;
_j2pul=393600;
_j3pul=288000;
_j4pul=360000;
_j5pul=360000;
_j6pul=132608;
////VELOCITY:
_ac=100000.0;
_de=100000.0;
_vpp=128000.0;
_vp=10;
////MODE:
_pve=8.887
_getCodeMode=0;
_runCodeMode=1;
_prmTPUL=200;
//REPOS
_rePosJ1=0;
_rePosJ2=0;
_rePosJ3=0;
_rePosJ4=0;
_rePosJ5=0;
_rePosJ6=0;
_sIRQ=0;
//LIMIT//==软件限位==
_sLp0=180
_sLn0=-180
_sLp1=120
_sLn1=-120
_sLp2=120
_sLn2=-120
_sLp3=180
_sLn3=-180
_sLp4=120
_sLn4=-120
_sLp5=360
_sLn5=-360

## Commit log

2019-07-25 Create CAD
2019-08-19 add big file
    [RobotAnnoV6PLUS_2018-8.STEP]
